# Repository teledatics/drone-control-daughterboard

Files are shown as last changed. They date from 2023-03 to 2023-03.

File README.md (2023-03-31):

# Drone Control

This is a hardware add-on 'lid' for the kimχ micro that adds drone control hardware
replacing a separate PX4 external embedded subsystem. The kimχ micro with the drone-
control add-on board is an all-in-one embedded drone and rover control system.

The kimχ micro with the drone-control add-on is an [i.MX8M Mini](https://www.nxp.com/products/processors-and-microcontrollers/arm-processors/i-mx-applications-processors/i-mx-8-applications-processors/i-mx-8m-mini-arm-cortex-a53-c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) Linux system with a 
32mm x 65mm x 10mm form factor.

drone control

drone control

## kimχ micro

kimχ micro is a small and spicy open hardware embedded SBC that offers tons of
versitility for many different applications.

[kimχ micro](https://github.com/groupgets/kimchi-micro)

kimchi micro

## Features

* m.2 connector for [NXP IW612](https://www.nxp.com/products/wireless/wi-fi-plus-bluetooth-plus-802-15-4/2-4-5-ghz-dual-band-1x1-wi-fi-6-802-11ax-plus-bluetooth-5-2-plus-802-15-4-tri-radio-solution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) Wi-Fi 6E/Bluetooth & BLE/Zigbee 802.15.4 board
* Gigabit Ethernet port
* ST Micro [ISM330DHCX](https://www.st.com/en/mems-and-sensors/ism330dhcx.html) IMU gyroscope/accelerometer
* ST Micro [IIS2MDC](https://www.st.com/en/mems-and-sensors/iis2mdc.html) magnetometer/compass
* Bosch [BMP581](https://www.bosch-sensortec.com/products/environmental-sensors/pressure-sensors/bmp581/) pressure sensor for altitude
* 15-pin Connector for Raspberry Pi v2 HD camera
* GPS & Telemetry connectors for NXP drone & rover kits
* PWM control for up to 8 external motors w/ NXP rover & drone kit compatible connector

## Work In Progress

Stay tuned for updates to both the hardware and software as we add features and port
PX4 Autopilot to the i.MX8M Mini on-board embedded ARM m4 core

Please see our Drone Control Yocto github repository to build a Linux OS for the kimχ 
micro with drone-control daughterboard

[Drone Control Yocto](https://github.com/teledatics/drone-control-yocto)

## Drone Control Components

The Drone Control components for a complete system.

* kimχ micro i.MX8M Mini SBC
* drone control add-on board
* NXP IW612 Wi-Fi/BT/802.15.4 m.2 card
* Teledatics 802.11ah HaLow long range mini-PCIe Wi-Fi card
* Raspberry Pi v2 camera

drone control components

## Assembled Ready To Fly

32mm x 65mm x 15mm assembled drone control kit ready to mount on an NXP drone or rover kit.

drone control components

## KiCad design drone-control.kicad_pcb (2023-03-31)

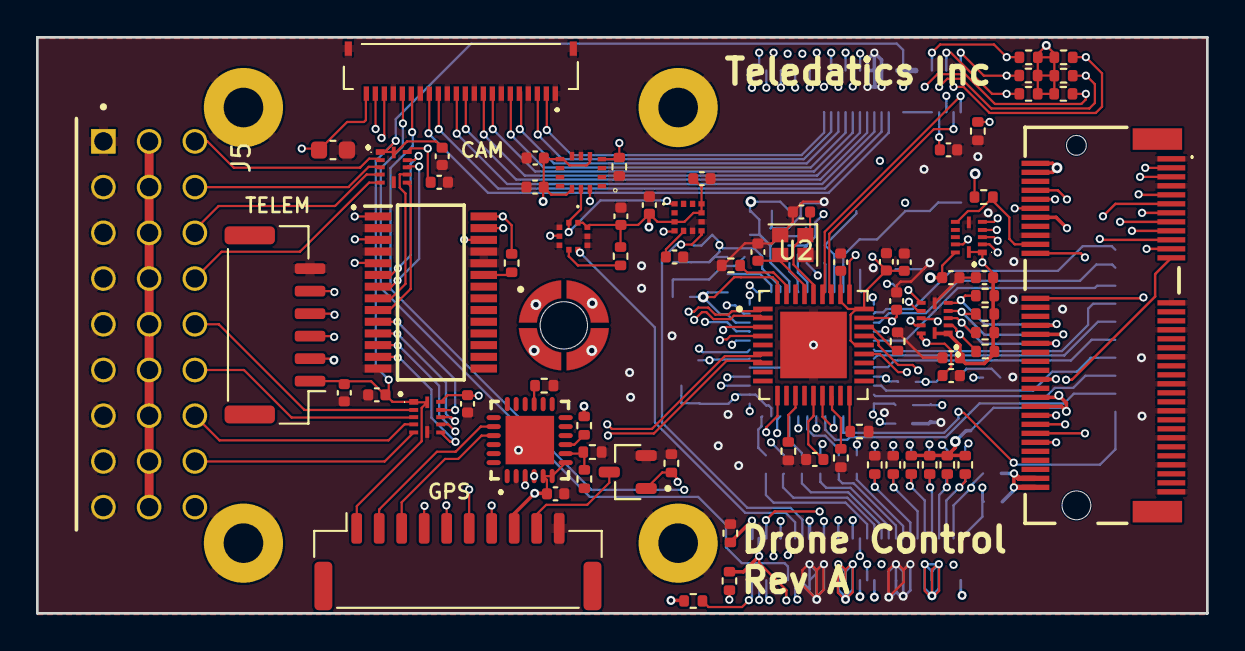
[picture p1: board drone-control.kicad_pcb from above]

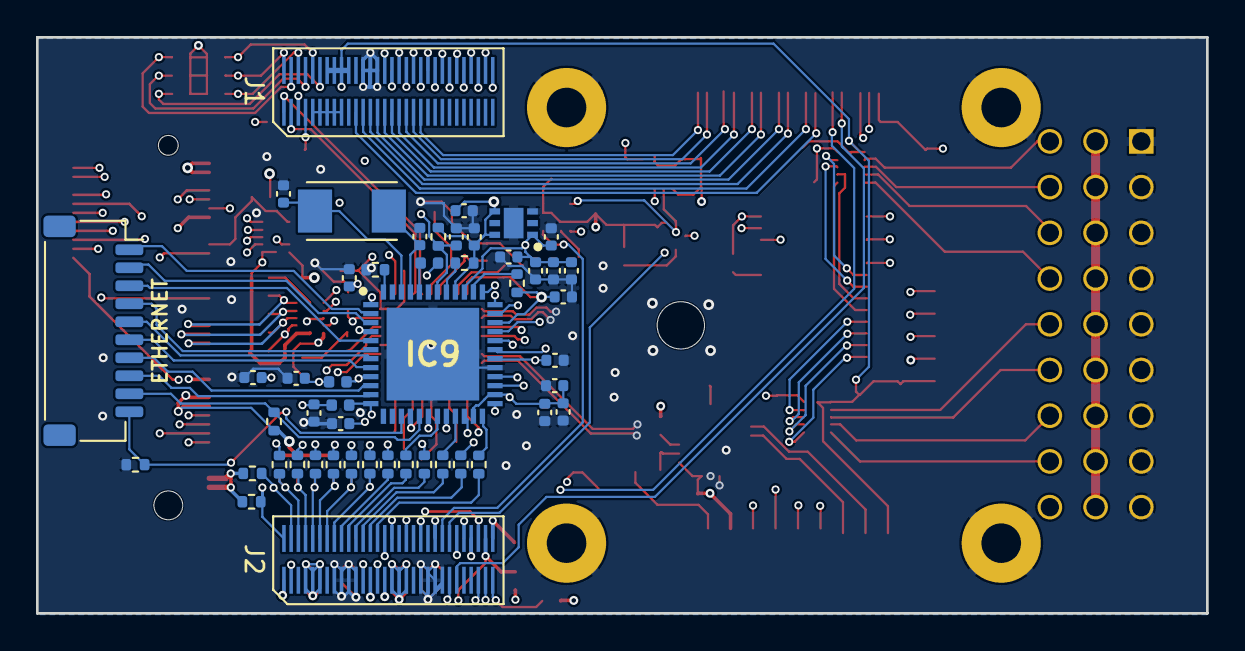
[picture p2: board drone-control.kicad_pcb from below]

Board: 6 copper layers, 65.0 x 32.0 mm, 131 parts (54 on the bottom side), 153 nets.

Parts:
C1, C2, C3, C4, C6, C7, C8, C9, C12, C13, C14, C17, C19, C20, C21, C27, C28, C29, C30, C31, C32, C33, C34, C35, C36, C37, C38, C40, C41, C42, C43: 100n; C_0402_1005Metric
C5: 4.7uF X5R 6.3V; C_0603_1608Metric
C10, C25, C26: 1u; C_0402_1005Metric
C11, C47, C53: 1uF; C_0402_1005Metric
C15, C16: 18pf; C_0402_1005Metric
C18: 220pf; C_0402_1005Metric
C22: 22u; C_0402_1005Metric
C23, C24: 18p; C_0402_1005Metric
C39: 4.7u; C_0402_1005Metric
FB1, FB2, FB3: 100MHz; L_0402_1005Metric
G1: teledatics_logo; teledatics_logo_kicad_footprint
H1, H2, H3, H4: MountingHole_Pad; MountingHole_2.2mm_M2_Pad
IC1, IC2, IC4, IC5: NTS0104GU12,115; NTS0104GU12115
IC3: PCA9685PW,112; SOP65P640X110-28N
IC6: ISM330DHCXTR; LGA-14_2.5X3X0.86_
IC7: IIS2MDCTR
IC8: CP2102N-A02-GQFN24R; QFN-24_L4.0-W4.0-P0.50-TL-EP2.6
IC9: KSZ9131RNXC; QFN50P700X700X90-49N
IC10: TLV75712PDRVR; SON65P200X200X80-7N
J1, J2: DF40HC(3.5)-60DS
J3: Bus_M.2_Socket_E; MDT420E03001
J5: TSW-109-08-T-T-RA; SAMTEC_TSW-109-08-T-T-RA
J6: GPS_EXT; JST_GH_SM10B-GHS-TB_1x10-1MP_P1.25mm_Horizontal
J7: Telem; JST_GH_BM06B-GHS-TBT_1x06-1MP_P1.25mm_Vertical
J8: Ethernet_Conn; JST_SH_SM10B-SRSS-TB_1x10-1MP_P1.00mm_Horizontal
J9: FH19SC-22S-0.5SH_09_; FH19SC22S05SH09
MP1: M.2 Standoff; JAE_SM3ZS067U410-NUT1-R1200
Q1: DMN3042L-7; SOT91P240X110-3N
R1, R4, R5, R6, R7, R13, R18, R19, R21, R26, R27, R28, R33: 100K; R_0402_1005Metric
R2, R3, R8, R9, R10, R11, R12, R16, R31, R46, R47, R48, R49, R52, R56, R57: 10K; R_0402_1005Metric
R14, R25, R50, R51, R53, R54, R55: 1K; R_0402_1005Metric
R15: 6.04K 1%; R_0402_1005Metric
R17: 47K; R_0402_1005Metric
R20: 4K7; R_0402_1005Metric
R22: 2K; R_0402_1005Metric
R23: 22K; R_0402_1005Metric
R24, R35, R36, R37, R38, R39, R40, R41, R42, R43, R44, R45: 22R; R_0402_1005Metric
R29: 12K 1%; R_0402_1005Metric
U1: BMP581
U2: USB2533I-1080AEN; QFN50P600X600X100-37N
Y1: ABM3-25.000MHZ-D2Y-T; XTAL_ABM3-25.000MHZ-D2Y-T
Y2: 24 MHz; Crystal_SMD_2016-4Pin_2.0x1.6mm

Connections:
/CAM_CK_N: J1.45, J9.8
/CAM_CK_P: J1.46, J9.9
/CAM_D0_N: J1.41, J9.2
/CAM_D0_P: J1.42, J9.3
/CAM_D1_N: J1.43, J9.5
/CAM_D1_P: J1.44, J9.6
/CAM_D2_N: J1.47, J9.11
/CAM_D2_P: J1.48, J9.12
/CAM_D3_N: J1.49, J9.14
/CAM_D3_P: J1.50, J9.15
/Connectors/BUZZER: J6.9, Q1.3
/ENET_MDC: IC9.36 (MDC), J2.2, R25.1
/ENET_MDIO: IC9.37 (MDIO), J2.1, R14.1
/ENET_RD0: J2.6, R36.2, R46.1
/ENET_RD1: J2.4, R37.2, R47.1
/ENET_RD2: J2.5, R38.2, R48.1
/ENET_RD3: J2.3, R39.2, R49.1
/ENET_RXC: J2.7, R24.2, R50.2
/ENET_RX_CTL: J2.8, R35.2, R51.2
/ENET_TD0: J2.10, R41.2
/ENET_TD1: J2.9, R42.2
/ENET_TD2: J2.12, R43.2
/ENET_TD3: J2.11, R44.2
/ENET_TXC: J2.14, R45.2
/ENET_TX_CTL: J2.13, R40.2
/Ethernet/AVDDH: FB1.1, IC9.1 (AVDDH_1), IC9.12 (AVDDH_2)
/Ethernet/AVDDL: FB2.1, IC9.4 (AVDDL_1), IC9.9 (AVDDL_2)
/Ethernet/AVDPLL: FB3.1, IC9.44 (AVDDL_PLL)
/Ethernet/LED1: IC9.17 (LED1/PME_N1//PHYAD0), J8.9, R53.1
/Ethernet/LED2: IC9.15 (LED2/PHYAD1), J8.10, R54.1
/Ethernet/TRD1+: IC9.2 (TXRXP_A), J8.1
/Ethernet/TRD1-: IC9.3 (TXRXM_A), J8.2
/Ethernet/TRD2+: IC9.5 (TXRXP_B), J8.3
/Ethernet/TRD2-: IC9.6 (TXRXM_B), J8.4
/Ethernet/TRD3+: IC9.7 (TXRXP_C), J8.5
/Ethernet/TRD3-: IC9.8 (TXRXM_C), J8.6
/Ethernet/TRD4+: IC9.10 (TXRXP_D), J8.7
/Ethernet/TRD4-: IC9.11 (TXRXM_D), J8.8
/USB2_ID: J1.58, R28.2
/USDHC3_CLK: J1.2, J3.9 (SDIO_CLK), R4.1
/USDHC3_CMD: J1.1, J3.11 (SDIO_CMD), R5.1
/USDHC3_DATA0: J1.4, J3.13 (SDIO_DATA0), R6.1
/USDHC3_DATA1: J1.5, J3.15 (SDIO_DATA1), R7.1
/USDHC3_DATA2: J1.6, J3.17 (SDIO_DATA2), R26.1
/USDHC3_DATA3: J1.3, J3.19 (SDIO_DATA3), R27.1
BEC: J5.02, J5.05, J5.08, J5.11, J5.14, J5.17, J5.20, J5.23, J5.26
BT_WAKE_3V3: IC2.7 (B4), J3.20 (~UART_WAKE), R3.1
ECSPI2_MISO: IC1.8 (B3), J1.30
ECSPI2_MISO_1V8: IC1.4 (A3), J3.40 (VENDOR_DEFINED), R8.1
ECSPI2_MOSI: IC1.7 (B4), J1.29
ECSPI2_MOSI_1V8: IC1.5 (A4), J3.38 (VENDOR_DEFINED), R9.1
ECSPI2_SCLK: IC1.9 (B2), J1.27
ECSPI2_SCLK_1V8: IC1.3 (A2), J3.42 (VENDOR_DEFINED), R11.1
ECSPI2_SS0: IC1.10 (B1), J1.28
ECSPI2_SS0_1V8: IC1.2 (A1), J3.64 (RESERVED), R10.1
GND: C1.2, C2.2, C3.2, C4.2, C5.2, C6.2, C7.2, C8.2, C9.2, C10.1, C11.2, C12.2, C13.2, C14.1, C15.1, C16.1, C17.2, C18.2, C19.2, C20.2, C21.2, C22.1, C23.2, C24.2, C25.2, C26.2, C27.2, C28.2, C29.2, C30.2, C31.2, C32.2, C33.2, C34.2, C35.2, C36.2, C37.2, C38.2, C39.2, C40.2, C41.2, C42.2, C43.1, C47.2, C53.1, H1.1, H2.1, H3.1, H4.1, IC1.6 (GND), IC2.6 (GND), IC3.2 (A1), IC3.4 (A3), IC3.14 (VSS), IC3.24 (A5), IC3.25 (EXTCLK), IC4.6 (GND), IC5.6 (GND), IC6.6 (GND_1), IC6.7 (GND_2), IC7.6 (GND_1), IC7.8 (GND_2), IC8.2 (GND), IC8.25 (EPAD), IC9.29 (VSS), IC9.49 (P_VSS), IC10.3 (GND_1), IC10.7 (GND_2), J1.12, J1.13, J1.14, J2.38, J2.39, J2.40, J2.41, J2.50, J2.51, J2.52, J2.53, J3.1 (GND), J3.7 (GND), J3.18 (GND), J3.33 (GND), J3.34 (UART_CTS), J3.39 (GND), J3.45 (GND), J3.51 (GND), J3.57 (GND), J3.63 (GND), J3.69 (GND), J3.75 (GND), J5.01, J5.04, J5.07, J5.10, J5.13, J5.16, J5.19, J5.22, J5.25, J6.10, J7.6, J9.1, J9.4, J9.7, J9.10, J9.13, J9.16, J9.19, J9.MP1 (MH1), J9.MP2 (MH2), MP1.1, MP1.2, MP1.3, MP1.4, Q1.2, R1.2, R13.1, R15.1, R16.2, R17.2, R18.1, R19.1, R20.1, R28.1, R29.1, R33.1, R50.1, R51.1, R54.2, R57.2, U1.3 (VSS_1), U1.5 (SDO), U1.8 (VSS_2), U1.9 (VSS_3), U2.37 (VSS), Y2.2, Y2.4
GPIO1_01: J2.29, J3.21 (~SDIO_WAKE), R2.1
GPIO1_09: J2.28, J3.23 (~SDIO_RESET)
GPIO1_10: J2.27, J3.62 (~ALERT)
GPIO1_11: IC2.5 (A4), J2.26
GPIO1_12: J2.25, Q1.1, R57.1
GPIO1_13: J2.24, U1.7 (INT)
GPIO1_14: IC7.7 (INT/DRDY), J2.23
GPIO1_15: IC6.4 (INT1), J2.22, R20.2
GPIO5_06: J1.23, J6.6
GPIO5_07: J1.25, J6.7
GPS_RXD: IC8.21 (TXD), J6.3
GPS_TXD: IC8.20 (RXD), J6.2
GPS_USB_N: IC8.4 (D-), U2.6 (USBDN3_DM/~PRT_DIS_M3)
GPS_USB_P: IC8.3 (D+), U2.7 (USBDN3_DP/~PRT_DIS_P3)
I2C1_SCL: IC6.13 (SCL), IC7.1 (SCL/SPC), J1.22, U1.2 (SCK)
I2C1_SDA: IC6.14 (SDA), IC7.4 (SDA/SDI/SDO), J1.21, U1.4 (SDI)
I2C2_SCL: J1.20, J3.60 (I2C_CLK)
I2C2_SDA: J1.19, J3.58 (I2C_DATA)
I2C3_SCL: IC3.26 (SCL), J1.18, J9.20
I2C3_SDA: IC3.27 (SDA), J1.17, J9.21
I2C4_SCL: J1.16, J6.4, U2.24 (SCL/SMBCLK/~CFG_SEL0)
I2C4_SDA: J1.15, J6.5, U2.22 (SDA/SMBDATA/~NON_REM1)
M2_USB_N: J3.5 (USB_D-), U2.3 (USBDN2_DM/~PRT_DIS_M2)
M2_USB_P: J3.3 (USB_D+), U2.4 (USBDN2_DP/~PRT_DIS_P2)
unnamed: IC3.23 (~OE), R12.1
unnamed: C18.1, IC7.5 (C1)
unnamed: IC8.9 (RSTB), R22.2
unnamed: IC8.15 (SUSPENDB), R16.1
unnamed: IC8.8 (VBUS), R17.1, R23.2
unnamed: IC9.41 (CLK125_NDO/LED_MODE), R52.1
unnamed: IC9.38 (INT_N/PME_N2/ALLPHYAD), R56.1
unnamed: IC9.48 (ISET), R15.2
unnamed: IC9.35 (RXC/PHYAD2), R24.1
unnamed: IC9.32 (RXD0/MODE0), R36.1
unnamed: IC9.31 (RXD1/MODE1), R37.1
unnamed: IC9.28 (RXD2/MODE2), R38.1
unnamed: IC9.27 (RXD3/MODE3), R39.1
unnamed: IC9.33 (RX_CTL/CLK125_EN), R35.1
unnamed: IC9.24 (TXC), R45.1
unnamed: IC9.19 (TXD0), R41.1
unnamed: IC9.20 (TXD1), R42.1
unnamed: IC9.21 (TXD2), R43.1
unnamed: IC9.22 (TXD3), R44.1
unnamed: IC9.25 (TX_CTL), R40.1
unnamed: C23.1, IC9.46 (XI), Y1.1
unnamed: C24.1, IC9.45 (XO), Y1.2
unnamed: R21.1, U1.6 (CSB)
unnamed: R33.2, U2.25 (HS_IND/~CFG_SEL1)
unnamed: R13.2, U2.12 (PRTPWR1/PRTCTL1/~BC_EN1)
unnamed: R18.2, U2.16 (PRTPWR2/PRTCTL2/~BC_EN2)
unnamed: R19.2, U2.18 (PRTPWR3/PRTCTL3/~BC_EN3)
unnamed: R29.2, U2.35 (RBIAS)
unnamed: C10.2, U2.14 (VDDCR12)
unnamed: C16.2, U2.33 (XTAL1/REFCLK), Y2.3
unnamed: C15.2, U2.32 (XTAL2), Y2.1
PCIE_USB_D_N: J2.60, U2.1 (SWAP_USBDN1_DM/~PRT_DIS_M1)
PCIE_USB_D_P: J2.59, U2.2 (SWAP_USBDN1_DP/~PRT_DIS_P1)
PWM0_3v3: IC3.6 (LED0), IC4.10 (B1)
PWM0_5v: IC4.2 (A1), J5.03
PWM1_3v3: IC3.7 (LED1), IC4.9 (B2)
PWM1_5v: IC4.3 (A2), J5.06
PWM2_3v3: IC3.8 (LED2), IC4.8 (B3)
PWM2_5v: IC4.4 (A3), J5.09
PWM3_3v3: IC3.9 (LED3), IC4.7 (B4)
PWM3_5v: IC4.5 (A4), J5.12
PWM4_3v3: IC3.10 (LED4), IC5.10 (B1)
PWM4_5v: IC5.2 (A1), J5.15
PWM5_3v3: IC3.11 (LED5), IC5.9 (B2)
PWM5_5v: IC5.3 (A2), J5.18
PWM6_3v3: IC3.12 (LED6), IC5.8 (B3)
PWM6_5v: IC5.4 (A3), J5.21
PWM7_3v3: IC3.13 (LED7), IC5.7 (B4)
PWM7_5v: IC5.5 (A4), J5.24
REF_CLK_32KHz_3V3: IC2.10 (B1), J3.50 (SUSCLK)
REF_CLK_32KHz_GPIO01_00: IC2.2 (A1), J2.30, R1.1
SAI2_MCLK: J2.20, J3.8 (PCM_CLK/I2S_SCK)
SAI2_RXD0: J2.15, J3.14 (PCM_OUT/I2S_SD_OUT)
SAI2_TXD0: J2.18, J3.12 (PCM_IN/I2S_SD_IN)
SAI2_TXFS: J2.16, J3.10 (PCM_SYNC/I2S_WS)
SAI3_MCLK: J2.37, J9.17
SAI3_RXD: J2.33, U2.28 (SUSP_IND/LOCAL_PWR/~NON_REM0)
SAI3_TXC: C53.2, J2.31, R31.2, U2.26 (~RESET)
SAI3_TXD: C42.1, IC9.42 (RESET_N), J2.32, R55.1
SAI3_TXFS: J2.36, J9.18
UART1_RX: J2.47, J3.22 (UART_RXD)
UART1_TX: J2.46, J3.32 (UART_TXD)
UART3_CTS: J1.26, J7.4
UART3_RTS: J1.24, J7.5
UART3_RX: IC2.4 (A3), J2.49, J7.3
UART3_TX: IC2.3 (A2), J2.48, J7.2
USB2_DN: J1.59, U2.30 (FLEX_USBUP_DM)
USB2_DP: J1.60, U2.31 (FLEX_USBUP_DP)
VCHG: J1.52, J1.53, J1.54, J1.55, J1.56
VDD_1V8: C1.1, C2.1, C14.2, C17.1, C19.1, C20.1, C21.1, IC1.1 (VCC(A)), IC1.12 (OE), IC2.1 (VCC(A)), IC2.12 (OE), IC6.5 (VDDIO), IC6.8 (VDD), IC6.12 (CS), IC7.3 (CS), IC7.9 (VDD), IC7.10 (VDD_IO), J2.43, J2.44, J2.45, R2.2, R4.2, R5.2, R6.2, R7.2, R8.2, R9.2, R10.2, R11.2, R21.2, R26.2, R27.2, U1.1 (VDDIO), U1.10 (VDD)
VDD_3V3: C3.1, C4.1, C5.1, C7.1, C9.1, C11.1, C12.1, C13.1, C22.2, C25.1, C32.1, C33.1, C34.1, IC1.11 (VCC(B)), IC2.11 (VCC(B)), IC3.1 (A0), IC3.3 (A2), IC3.5 (A4), IC3.28 (VDD), IC4.11 (VCC(B)), IC5.11 (VCC(B)), IC8.5 (VIO), IC8.6 (VDD), IC8.7 (VREGIN), IC9.16 (DVDDH_1), IC9.34 (DVDDH_2), IC9.40 (DVDDH_3), IC10.4 (EN), IC10.6 (IN), J2.55, J2.56, J2.57, J3.2 (3.3V), J3.4 (3.3V), J3.54 (~W_DISABLE2), J3.56 (~W_DISABLE1), J3.72 (3.3V), J3.74 (3.3V), J6.8, J9.22, R3.2, R12.2, R14.2, R22.1, R25.2, R31.1, R46.2, R47.2, R48.2, R49.2, R52.2, R53.2, R55.2, R56.2, U2.10 (VDDA33), U2.15 (VDD33), U2.23 (VDD33), U2.27 (VBUS_DET/PIO16), U2.29 (VDDA33), U2.36 (VDDA33)
VDD_5V: C6.1, C8.1, C43.2, C47.1, IC4.1 (VCC(A)), IC4.12 (OE), IC5.1 (VCC(A)), IC5.12 (OE), J1.7, J1.8, J1.9, J1.10, J1.57, J6.1, J7.1
VDD_PHY_1V2: C26.1, C27.1, C28.1, C29.1, C30.1, C31.1, C35.1, C36.1, C37.1, C38.1, C39.1, C40.1, C41.1, FB1.2, FB2.2, FB3.2, IC9.18 (DVDDL_1), IC9.23 (DVDDL_2), IC9.26 (DVDDL_3), IC9.30 (DVDDL_4), IC9.39 (DVDDL_5), IC10.1 (OUT)

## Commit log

2023-03-31 move silkscreen to fab
    [drone-control.kicad_pcb]
2023-03-31 add RPi camera
